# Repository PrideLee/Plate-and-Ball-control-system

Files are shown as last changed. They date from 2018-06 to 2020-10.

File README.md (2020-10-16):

# Plate-and-Ball control system

- Based on steering engine control technology, PID (proportional plus integral plus derivative) control algorithm, images processing technology and single chip development, we design and achieve a plate-and-ball control system, which collects the ball position and motion information by a camera, as actuator, linkage mechanism driven by steering engine controls tilts the plate, then controling the ball to finish specific motion.
- Hardwares include camera stant, SCM development board, steering engine, OV7670 camera, linkage, keyboard and DC power supply.
- The system adopts PID control of a single loop strategy, camera collects the real position information and calculating the position deviation. Based on the deviation, we utilize PID algorithm to get the duty cycle of PWM, through this singnal to drive the steering engine, thus we can control the tilt of plate to plan the motion track of the ball.

**You can dowmload the full report from [here](https://github.com/PrideLee/Plate-and-Ball-control-system/blob/master/%E6%9D%BF%E7%90%83%E6%8E%A7%E5%88%B6%E7%B3%BB%E7%BB%9F.pdf).**
**There are also some demos, you can check them in this [link](https://github.com/PrideLee/Plate-and-Ball-control-system/tree/master/img%26video).**

## 摘要

本滚球系统以STM32F4单片机为核心，舵机作为执行机构，通过连杆机构使平板倾斜控制小球完成指定运动。结合舵机控制技术，PID控制算法，图形图像处理技术。硬件部分由支架、舵机、连杆、OV7670摄像头、键盘、直流电源、单片机等组成。系统采用单环PD控制，由摄像读取平板小球灰度图并转化为二值图，得到小球在平板上的坐标。舵机控制采用PWM占空比调制，由PD算法得到占空比，控制舵机转过一定角度以使平板倾斜，使小球完成各种动作。测试各项指标都符合要求。

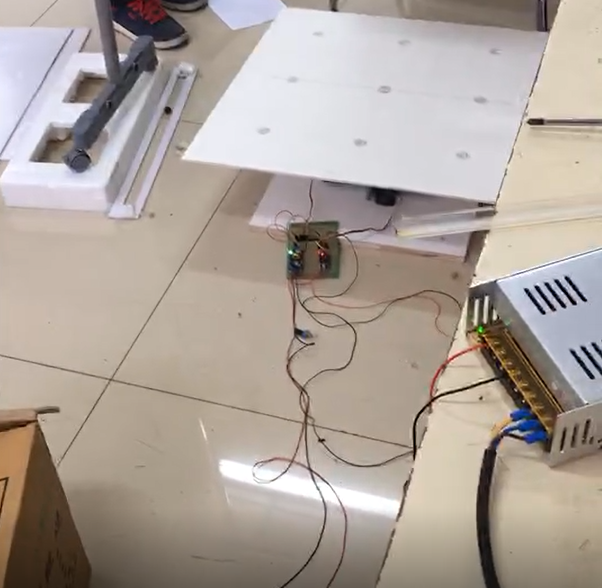
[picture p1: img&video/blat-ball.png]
#

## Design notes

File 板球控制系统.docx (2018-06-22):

摘要

本滚球系统以STM32F4单片机为核心，舵机作为执行机构，通过连杆机构使平板倾斜控制小球完成指定运动。结合舵机控制技术，PID控制算法，图形图像处理技术。硬件部分由支架、舵机、连杆、OV7670摄像头、键盘、直流电源、单片机等组成。系统采用单环PD控制，由摄像读取平板小球灰度图并转化为二值图，得到小球在平板上的坐标。舵机控制采用PWM占空比调制，由PD算法得到占空比，控制舵机转过一定角度以使平板倾斜，使小球完成各种动作。测试各项指标都符合要求。

关键词：滚球系统；单片机；PID控制；图像处理

一、系统方案

1.1技术路线

首先对平板设计支撑机构，保证平板绕X，Y两个轴旋转的自由度，平板运动的动力来自于舵机。由摄像头获取小球实时运动图像，通过单片机读取运动图像并进行二值化处理，获取小球位置坐标。并将小球的实时图像坐标与平板坐标转换至同一坐标系。控制策略采用单环PID控制，对小球的位置坐标与期望位置之差做运算，输出量生成舵机PWM控制占空比，对平板进行控制。[1]

1.2系统结构

图1系统结构示意

滚球控制系统机械机构如上图所示。舵机固定在底座木板上，保证两电机相互垂直。平板中心处用万向节作为主支撑，舵机通过连杆机构与万向节连接支撑平板。

采用龙门型支架，将摄像头安置于横梁中间，控制部分位于支架上部，以缩短摄像头数据传输线路。

1.3 方案论证

1.3.1电机的选择

方案一：步进电机。步进电机的角度控制精度高，但容易丢步，扭力小，且不易设计机械结构。

方案二：舵机。舵机扭力大，舵机有配套的舵机臂，连杆机构容易设计，控制方便且精确。

考虑到步进电机机械结构不易设计，且会有丢步的可能，导致控制精度降低，因此选择型号为MG958高扭力数码舵机，其扭力为，速度为。

1.3.2平板的选择

方案一：木板。木板较重，舵机的支撑负担较重，且表面光滑度一般，不利于小球的滚动，影响精度。

方案二：KT板。KT板重量轻，且强度满足要求，表面平整度高，有利于小球的精确控制。

为了降低舵机驱动负担，板材应在保证强度的情况下尽可能轻，选择KT板。

1.3.3 电源的选择

方案一：采用电池供电，电池供电可以增加设备的便携性，但是本装置最大瞬间电流可达4A，电压达到6V，普通电池难以承受巨大电流，且电量会迅速耗尽，电压会出现下降，使得舵机动力下降，影响滚球的精确控制。

方案二：采用开关电源与降压模块。开关电源把220v市电转化为12V电流电压稳定输出，可以长时间以稳定电压电流工作,能承受较大电压电流。降压模块将12V电压转换为5V，性能稳定。

考虑到本系统调试过程较长，且无需经常移动，因此选择开关电源配合降压模块供电。

1.3.4 控制方案的选择

方案一：采用LQR优化算法。LQR线性二次型最优控制算法能够较好地兼顾系统的鲁棒稳定性和快速性，而且不必根据要求的性能确定闭环极点的位置，只需要根据系统的响应曲线寻找出合适的状态变量和控制量的加权矩阵即可，控制效果好。但LQR在设计中运算量很大，不适合单片机运行。

方案二：采用PID控制算法。该算法原理简单，使用方便，适应性强。而且PID算法有一套完整的参数整定与设计方法，易于掌握，在重视系统的可靠性时，使用PID控制能获得较高的性价比。

本系统的控制核心为STM32单片机，需要同时处理图像与控制，为了降低单片机的运算负担，所以选择PID控制算法[²]。

二、理论分析与计算

2.1 小球检测及处理

采用摄像头检测小球的实时位置,读取出平板小球的灰度图，并转为二值图[3]。如下所示，图形中白色区域为平板，黑色小点为小球。经二值化后的图像其数值均为0和1。黑色为0，白色为1。检查图像矩阵中的0元素即为小球在图像坐标系中的位置坐标，将小球的每个像素点坐标取平均得到小球的中心坐标。设置摄像头每秒读取30帧图像以实时跟踪小球坐标。输入小球运动的理想坐标，通过PID算法控制小球的运动。

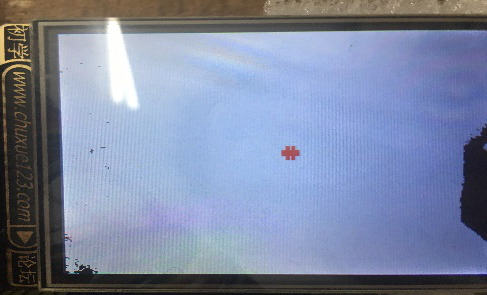
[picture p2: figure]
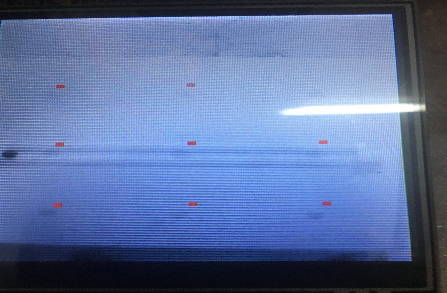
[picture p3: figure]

图2 小球检测灰度图 图3 小球检测二值图

2.2 控制方法分析

本系统采用PID算法来控制舵机转动的角度，进而控制平板和小球的运动。摄像头采集小球的位置坐标，并与期望位置坐标比较，PID运算的输出控制舵机 转动，使得小球完成期望运动[⁴]。PID控制公式如下所示。

小球位置偏差e（t）与算法输出U（t)的关系为：

4

1

3

其传递函数为：

三、电路与程序设计

3.1 电路设计与参数计算

电路由电源、电机控制、单片机最小系统、液晶显示、摄像头、按键部分组成。电源采用开关电源与DC-DC降压模块组合，液晶与摄像头的线路为多组控制线与数据线。下图为单片机最小系统、舵机和按键部分电路。

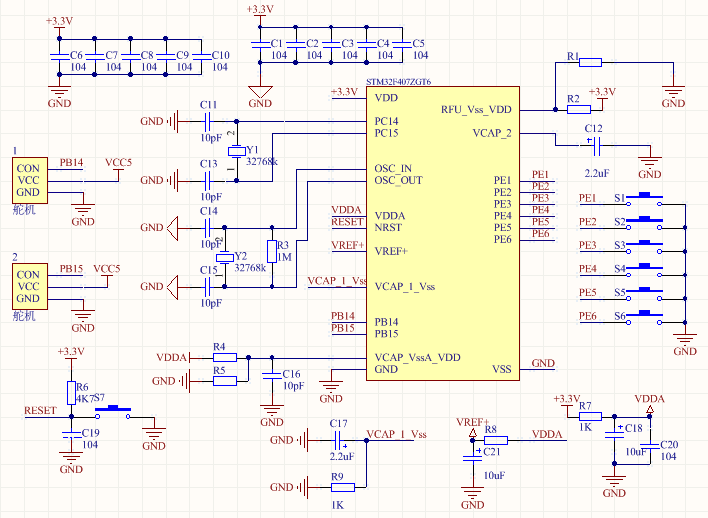
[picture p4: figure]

图4单片机、按键、舵机部分电路

开关电源12V，经过稳压模块后转为5V，控制部分与动力部分分开供电。

3.2程序流程

图5执行机构控制流程

四、测试结果

4.1测试方法

测试时，通过按键控制依次执行各项要求，对每一项指标都多次测试，准确记录测试数据。

4.2测试数据

4.2.1基本部分测试数据

基本部分测试数据见附录1

4.2.2发挥部分测试数据

发挥部分测试数据见附录2

4.2.3测试结果分析

通过对各项指标的多次测试，所设计系统可以完成测试要求指标。

五、参考文献

[1] 白明.非线性板球系统解耦与控制算法研究[D].吉林大学.2008.

[2] 张洋，刘军，严汉宇，左忠凯.精通STM32F4（库函数版）[B].北京：北京航空航天大学出版社.2015.

[3] 胡琳静,赵世敏,孙政顺. 基于模糊控制的板球控制系统实验装置[J].实验技术与管理.2005,25(4):16-19.

[4] 何芝强. PID控制器参数整定方法及其应用研究[M].浙江大学.2005.

六、附录

附录1

表1基本要求1测试数据

次数 指标 | 1 | 2 | 3 | 4 | 5
停留时间 | 无限 | 无限 | 无限 | 无限 | 无限

表2基本要求2测试数据

次数 指标 | 1 | 2 | 3 | 4 | 5
是否进入区域5 | 是 | 是 | 是 | 是 | 是
区域5停留时间 | 3s | 3s | 3s | 3s | 3s
总时间 | 14s | 16s | 13s | 12s | 4s

表3基本要求3测试数据

次数 指标 | 1 | 2 | 3 | 4 | 5
是否进入区域4 | 是 | 是 | 是 | 是 | 是
区域4停留时间 | 3s | 3s | 3s | 4s | 2s
是否进入区域5 | 是 | 是 | 是 | 是 | 是
区域5停留时间 | 3s | 4s | 3s | 4s | 2s
总时间 | 13s | 12s | 15s | 14s | 14s

表4基本要求4测试数据

次数 指标 | 1 | 2 | 3 | 4 | 5
是否进入区域9 | 是 | 是 | 是 | 是 | 是
区域9停留时间 | 3s | 2s | 4s | 2s | 3s
总时间 | 30s | 28s | 27s | 30s | 33s

附录2

表5发挥部分1测试数据

次数 指标 | 1 | 2 | 3 | 4 | 5
是否进入区域2、6 | 是 | 是 | 是 | 是 | 是
是否停止于区域9 | 是 | 是 | 是 | 是 | 是
区域9停留时间 | 3s | 2s | 3s | 4s | 2s

表6发挥部分2测试数据

次数 指标 | 1 | 2 | 3 | 4 | 5
是否进入各区域 | 是 | 是 | 是 | 是 | 是

表7发挥部分3测试数据

次数 指标 | 1 | 2 | 3 | 4 | 5
运动圈数 | 4 | 3 | 3 | 2 | 4
是否停止于区域9 | 是 | 是 | 是 | 是 | 是
区域9停留时间 | 3s | 4s | 4s | 3s | 3s

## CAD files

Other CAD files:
mechanical structure/摆杆.dwg
mechanical structure/摇臂.dwg

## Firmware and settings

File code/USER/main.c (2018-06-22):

#include "stm32f4xx.h" 

#include "sys.h"
#include "delay.h"
#include "usart.h"
#include "usart3.h"	

#include "FreeRTOS.h"
#include "task.h"

#include "APP.h"
#include "APPinit.h"
#include "BEED.h" 
#include "LED.h"
#include "KEY.h"
#include "ServoPWMOut.h"
#include "lcd.h"
#include "Timer.h"

#include "Function.h"
/************************************************/

void _Test_(void);//（此函数用于硬件测试，不经过FreeRTOS）


uint8_t Debug=1;//默认开启调试输出
uint8_t tasknum=0;

uint8_t use_freertos=1;//在输出中用
/************************************************/

int main()
{
	uint8_t i=1;
	
	NVIC_PriorityGroupConfig(NVIC_PriorityGroup_4);
	
	delay_init(168);
	uart_init(115200);
	uart3_init(9600);
	
	LED_Init();
	BEED_Init(1);
	KEY_Init();
	
	PWMOut_TIM12(2000,840,1000);
	Timer20msInit();//FreeRTOS系统定时      
	
	LCD_Init();
	LCD_DisplayOn();
	LCD_Clear(BLACK);
	LCD_AUTOScan_Dir(L2R_U2D);
	LCD_DisplayString_color(50,50,12,"This is my OV7670 test!",WHITE,BLACK);
	LCD_Display_Dir(0);
	
////////////////////////////////////
taskENTER_CRITICAL();           //进入临界区
	if(OV7670_Init()){ LED1=0;LED0=0; }
taskEXIT_CRITICAL();            //退出临界区
	
	Coordinate_Init();//坐标初始化
		
	OV7670_Light_Mode(3);//白平衡设置//0:自动//1:太阳sunny//2,阴天cloudy//3,办公室office//4,家里home
	OV7670_Color_Saturation(4);//色度 0/-2  1/-1  2/0  3/1  4/2
	OV7670_Brightness(2);//亮度 0/-2  1/-1  2/0  3/1  4/2
	OV7670_Contrast(4);//对比度 0/-2  1/-1  2/0  3/1  4/2
	OV7670_Special_Effects(0);//0:普通模式//1,负片//2,黑白//3,偏红色//4,偏绿色//5,偏蓝色//6,复古	 

	printf("OV7670 OK\n");
	printf_3_("OK\n",3);
	LCD_DisplayString(10,10,12,"Ready");
	
	while(i)//是否开启调试
	{
		if(KEY_Scan(1))
		{
			LCD_DisplayString(80,10,12,"Debug");
			i=0;
			BEED_1(50);
			Debug=1;
		}
		if(KEY_Scan(2))
		{
			i=0;
			BEED_1(50);
			Debug=0;
		}
	}
	
	LCD_Display_Dir(0);
	LCD_AUTOScan_Dir(L2R_U2D);
	
	AllAppInit();
	
	vTaskStartScheduler();          //开启任务调度
	
	while(1)
	{
		;
	}
}

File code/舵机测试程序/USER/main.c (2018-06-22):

#include "stm32f4xx.h"
#include "usart.h"
#include "delay.h"
#include "ServoPWMOut.h"
#include "LED.h"

void Set_MotoDeg(uint16_t speed, uint8_t num);
void SetTIM12Compare_ (uint16_t Data, uint8_t Channel);

int main(void)
{
	u32 t=8500,j=0,i=0;
	uart_init(115200);
	delay_init(168);
	PWMOut_TIM12(48000,7,15000);
	LED_Init();
	
	LED0=0;
	
  while(1)
	{
		if(t==8500)    { j=1; }
		if(t==21500) { j=0; }
		
		if(j) t+=10;
		else t-=10;
		
		Set_MotoDeg(t,1);
		Set_MotoDeg(t,2);
		
		printf("%d\n",t);
		delay_ms(5);
		
		i++;
		if(i==10)
		{
			LED0=~LED0;
			LED1=~LED1;
			i=0;
		}
		
	}
}

void Set_MotoDeg(uint16_t speed, uint8_t num)
{
	if(speed>2500)speed=2500;
  SetTIM12Compare_ (speed, num);
}


void SetTIM12Compare_ (uint16_t Data, uint8_t Channel)
{
	if(Channel==1)TIM_SetCompare1 (TIM12,Data);
	else  if(Channel==2)TIM_SetCompare2 (TIM12,Data);
}

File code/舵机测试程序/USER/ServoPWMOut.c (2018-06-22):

/*
	TIM9  :PE 5  6
	TIM12 :PB 14 15
*/

#include "ServoPWMOut.h"

uint16_t g_Period_TIM9=0;
uint16_t g_Period_TIM12=0;

/* 
	功能：一般PWM输出设置，TIM9
	输入：Period			：周期
				Prescaler		：分频值
				Duty				：占空比（非百分比制）
	输出：无
	备注：168MHz
*/
void PWMOut_TIM9(uint16_t Period, uint16_t Prescaler, uint16_t Duty)
{
	GPIO_InitTypeDef GPIO_I;
	TIM_TimeBaseInitTypeDef TIM_TimeBaseI;
	TIM_OCInitTypeDef TIM_OCI;
	
	RCC_AHB1PeriphClockCmd (RCC_AHB1Periph_GPIOE,	ENABLE);
	
	GPIO_PinAFConfig (GPIOE,GPIO_PinSource5,  GPIO_AF_TIM9);
	GPIO_PinAFConfig (GPIOE,GPIO_PinSource6,  GPIO_AF_TIM9);
	
	GPIO_I.GPIO_Mode=GPIO_Mode_AF ;
	GPIO_I.GPIO_OType=GPIO_OType_PP ;
	GPIO_I.GPIO_Pin=GPIO_Pin_5|GPIO_Pin_6;
	GPIO_I.GPIO_PuPd=GPIO_PuPd_UP ;
	GPIO_I.GPIO_Speed=GPIO_High_Speed ;
	GPIO_Init (GPIOE,&GPIO_I);
	
	RCC_APB2PeriphClockCmd (RCC_APB2Periph_TIM9,ENABLE);
	
	g_Period_TIM9=Period;
	
	TIM_TimeBaseI.TIM_ClockDivision=TIM_CKD_DIV1;
	TIM_TimeBaseI.TIM_CounterMode=TIM_CounterMode_Up;
	TIM_TimeBaseI.TIM_Period=Period-1;
	TIM_TimeBaseI.TIM_Prescaler=Prescaler-1;  
	TIM_TimeBaseInit (TIM9,&TIM_TimeBaseI);
	
//	TIM_OCI.TIM_OCIdleState=
	TIM_OCI.TIM_OCMode=TIM_OCMode_PWM1;
//	TIM_OCI.TIM_OCNIdleState=
//	TIM_OCI.TIM_OCNPolarity=
	TIM_OCI.TIM_OCPolarity=TIM_OCPolarity_High;
//	TIM_OCI.TIM_OutputNState=
	TIM_OCI.TIM_OutputState=TIM_OutputState_Enable;
	TIM_OCI.TIM_Pulse=Duty;
	TIM_OC1Init (TIM9,&TIM_OCI);
	TIM_OC2Init (TIM9,&TIM_OCI);
	
	TIM_OC1PreloadConfig (TIM9,ENABLE);
	TIM_ARRPreloadConfig (TIM9,ENABLE);
	
	TIM_Cmd(TIM9,ENABLE);
}

/* 
	功能：一般PWM输出设置，TIM12
	输入：Period			：周期
				Prescaler		：分频值
				Duty				：占空比（非百分比制）
	输出：无
	备注：84MHz
*/
void PWMOut_TIM12(uint16_t Period, uint16_t Prescaler, uint16_t Duty)
{
	GPIO_InitTypeDef GPIO_I;
	TIM_TimeBaseInitTypeDef TIM_TimeBaseI;
	TIM_OCInitTypeDef TIM_OCI;
	
	RCC_AHB1PeriphClockCmd (RCC_AHB1Periph_GPIOB,	ENABLE);
	
	GPIO_PinAFConfig (GPIOB,GPIO_PinSource14,  GPIO_AF_TIM12);
	GPIO_PinAFConfig (GPIOB,GPIO_PinSource15,  GPIO_AF_TIM12);
	
	GPIO_I.GPIO_Mode=GPIO_Mode_AF ;
	GPIO_I.GPIO_OType=GPIO_OType_PP ;
	GPIO_I.GPIO_Pin=GPIO_Pin_14|GPIO_Pin_15;
	GPIO_I.GPIO_PuPd=GPIO_PuPd_UP ;
	GPIO_I.GPIO_Speed=GPIO_High_Speed ;
	GPIO_Init (GPIOB,&GPIO_I);
	
	RCC_APB1PeriphClockCmd (RCC_APB1Periph_TIM12,ENABLE);
	
	g_Period_TIM12=Period;
	
	TIM_TimeBaseI.TIM_ClockDivision=TIM_CKD_DIV1;
	TIM_TimeBaseI.TIM_CounterMode=TIM_CounterMode_Up;
	TIM_TimeBaseI.TIM_Period=Period-1;
	TIM_TimeBaseI.TIM_Prescaler=Prescaler-1;  
	TIM_TimeBaseInit (TIM12,&TIM_TimeBaseI);
	
//	TIM_OCI.TIM_OCIdleState=
	TIM_OCI.TIM_OCMode=TIM_OCMode_PWM1;
//	TIM_OCI.TIM_OCNIdleState=
//	TIM_OCI.TIM_OCNPolarity=
	TIM_OCI.TIM_OCPolarity=TIM_OCPolarity_High;
//	TIM_OCI.TIM_OutputNState=
	TIM_OCI.TIM_OutputState=TIM_OutputState_Enable;
	TIM_OCI.TIM_Pulse=Duty;
	TIM_OC1Init (TIM12,&TIM_OCI);
	TIM_OC2Init (TIM12,&TIM_OCI);
	
	TIM_OC1PreloadConfig (TIM12,ENABLE);
	TIM_OC2PreloadConfig (TIM12,ENABLE);
	TIM_ARRPreloadConfig (TIM12,ENABLE);
	
	TIM_Cmd(TIM12,ENABLE);
}

/* 
	功能：TIM9占空比设置
	输入：Duty				：占空比（百分比制）
				Channel     ：通道
	输出：无
*/
void SetPWMDuty_TIM9(uint8_t Duty, uint8_t Channel)
{
	uint16_t duty=0;
	duty=Duty*(g_Period_TIM9-1)/100;
	if(Channel==1)TIM_SetCompare1 (TIM9,duty);
	else if(Channel==2)TIM_SetCompare2 (TIM9,duty);
	
}
/* 
	功能：TIM12占空比设置
	输入：Duty				：占空比（百分比制）
				Channel     ：通道
	输出：无
*/
void SetPWMDuty_TIM12(uint8_t Duty, uint8_t Channel)
{
	uint16_t duty=0;
	duty=Duty*(g_Period_TIM12-1)/100;
	if(Channel==1)TIM_SetCompare1 (TIM12,duty);
	else if(Channel==2)TIM_SetCompare2 (TIM12,duty);
}

/* 
	功能：TIM9周期/频率设置
	输入：Period				：周期
				Prescaler     ：分频值
        ChangePSC			：是否改变分频值  1 change  0 no change
	输出：无
*/
void TIM9Change(uint16_t Period, uint16_t Prescaler, uint8_t ChangePSC)
{
	TIM_SetAutoreload (TIM9,Period-1);
	g_Period_TIM9=Period;
	if(ChangePSC)TIM_PrescalerConfig (TIM9,Prescaler-1,TIM_PSCReloadMode_Update);
}
/* 
	功能：TIM12周期/频率设置
	输入：Period				：周期
				Prescaler     ：分频值
        ChangePSC			：是否改变分频值  1 change  0 no change
	输出：无
*/
void TIM12Change(uint16_t Period, uint16_t Prescaler, uint8_t ChangePSC)
{
	TIM_SetAutoreload (TIM12,Period-1);
	g_Period_TIM12=Period;
	if(ChangePSC)TIM_PrescalerConfig (TIM12,Prescaler-1,TIM_PSCReloadMode_Update);
}

/* 
	功能：直接调TIM9比较寄存器
	输入：Data				：新值
				Channel     ：通道 1 or 2
	输出：无
*/
void SetTIM9Compare (uint16_t Data, uint8_t Channel)
{
	if(Channel==1)TIM_SetCompare1 (TIM9,Data);
	else  if(Channel==2)TIM_SetCompare2 (TIM9,Data);
}
/* 
	功能：直接调TIM12比较寄存器
	输入：Data				：新值
				Channel     ：通道 1 or 2
	输出：无
*/
void SetTIM12Compare (uint16_t Data, uint8_t Channel)
{
	if(Channel==1)TIM_SetCompare1 (TIM12,Data);
	else  if(Channel==2)TIM_SetCompare2 (TIM12,Data);
}
